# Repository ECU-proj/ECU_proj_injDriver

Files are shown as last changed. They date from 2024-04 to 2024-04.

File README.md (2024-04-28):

# ECU Project

   

The injector driver is an integral part of a broader project aimed at creating a fully customizable Engine Control Unit (ECU). The project’s objective is to provide a versatile tool capable of handling everything from straightforward retrofits to professional scenarios where writing custom software tailored to specific applications is essential. Both the hardware and software components are entirely open source and compatible with professional interfaces, representing the cutting edge in the field of engine and vehicle control

## Dual Injector Driver - Alpha Hardware put in production

The injection stage is a fundamental and delicate component of engine control systems. There are two types of injectors:

High Impedance: Usually, Port Fuel Injection (PFI) injectors have a high-impedance solenoid, which automatically limits the current, albeit at the expense of opening speed and precision.
Low Impedance: Typically, newer Gasoline Direct Injection (GDI) injectors require current control and are more sophisticated. A low impedance driver can drive an high impedance injector with simpler software



The driver mainly focus on injectors, while it will used in other applications also, such as GDI pumps actuations, trasmission solenoids, ....

### Injector Driver Hardware

The injector driver hardware is based on the new TI H-Bridge IC DRV8262 controlled by an Attiny 1624
The driver is capable of 70V and 8A peak in dual configuration (two injectors per driver), which is more than enough for the injectors I had experience on.
The board features a high/low voltage switch for correctly implementing the V boost logic. As the supply switch is in common, controlling the voltage on both the injectors in the same time is not possible. Injection number must be carefully assigned in order to avoid control overlap




### Injector Driver Software

Input: logic pulse corresponding to Injection time from ecu
Output: PID control of the current through the injectors

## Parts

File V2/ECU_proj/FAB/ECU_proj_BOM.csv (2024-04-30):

Id | Riferimento | Impronta | Quantità | Valore | Produttore
1 | J1 | MountingHole_3.2mm_M3_ISO7380_Pad_TopBottom | 1 | OUT1
2 | C12,C14 | C_0402_1005Metric | 2 | 4.7uF
3 | Q1,Q2 | IRF9530NSTRLPBF | 2 | IRF9530NSTRLPBF
4 | C13,C10 | C_0402_1005Metric | 2 | 0.1uF
5 | J9 | MountingHole_3.2mm_M3_ISO7380_Pad_TopBottom | 1 | 48V
6 | U1 | SOIC-14_3.9x8.7mm_P1.27mm | 1 | ATtiny1624-SS
7 | C23 | C_0402_1005Metric | 1 | 1uF
8 | C17,C11,C20,C15,C16,C19,C18,C21 | C_0402_1005Metric | 8 | 10uF
9 | R6,R5 | C_0402_1005Metric | 2 | 1.6k
10 | J10 | PinHeader_2x03_P1.27mm_Vertical | 1 | Conn_02x03_Odd_Even
11 | D2 | LED_0402_1005Metric | 1 | LED
12 | C5,C8,C3,C7,C4,C2 | C_0402_1005Metric | 6 | 1nF 100V
13 | J2 | MountingHole_3.2mm_M3_ISO7380_Pad_TopBottom | 1 | OUT2
14 | J5 | MountingHole_3.2mm_M3_ISO7380_Pad_TopBottom | 1 | GND
15 | J7 | MountingHole_3.2mm_M3_ISO7380_Pad_TopBottom | 1 | 3.3V
16 | C1,C6 | C_0402_1005Metric | 2 | 10nF 100V
17 | IC2 | TC4422SOIC127P600X175-8N | 1 | TC4421AVOA
18 | C22 | CP_Elec_8x11.9 | 1 | C_Polarized
19 | J3 | MountingHole_3.2mm_M3_ISO7380_Pad_TopBottom | 1 | OUT4
20 | C9,C25 | C_0402_1005Metric | 2 | 100nF 100V
21 | C24 | C_0402_1005Metric | 1 | 1uF 100V
22 | J4 | MountingHole_3.2mm_M3_ISO7380_Pad_TopBottom | 1 | OUT3
23 | D1 | V20DM100C | 1 | V20DM100C-M3_I
24 | J8 | MountingHole_3.2mm_M3_ISO7380_Pad_TopBottom | 1 | 12V
25 | R3,R1 | C_0402_1005Metric | 2 | 0.75
26 | IC1 | DRV8262 | 1 | DRV8262DDWR
27 | IC3 | TC4422SOIC127P600X175-8N | 1 | TC4422AVOA
28 | J11 | PinHeader_1x01_P1.00mm_Vertical | 1 | Conn_01x01
29 | J6 | MountingHole_3.2mm_M3_ISO7380_Pad_TopBottom | 1 | PGND
30 | R2,R4 | C_0402_1005Metric | 2 | 100k
31 | R7 | C_0402_1005Metric | 1 | 10k

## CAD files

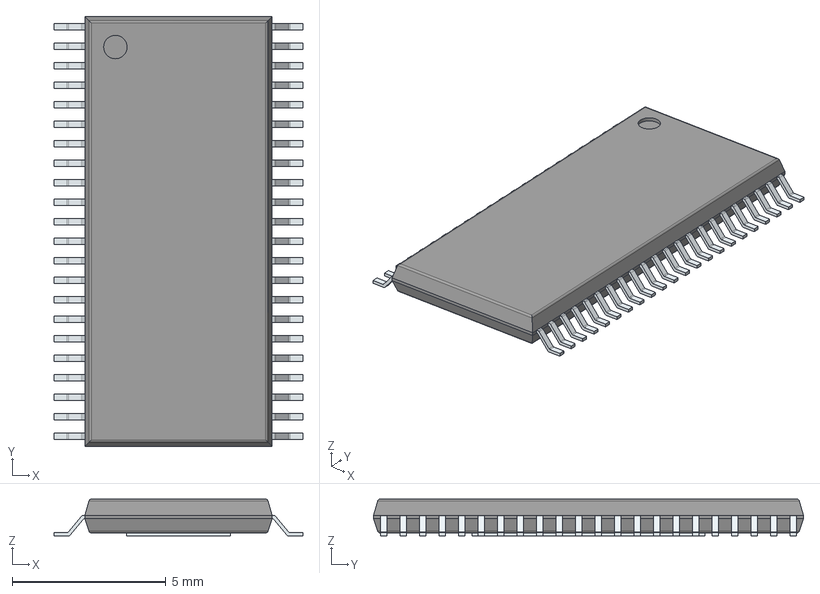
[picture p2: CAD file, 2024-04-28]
V2/LIB_DRV8262DDWR/DRV8262DDWR/3D/DRV8262DDWR.stp
8.10 x 14.0 x 1.20 mm
PinsArrayLR
ThermalPad

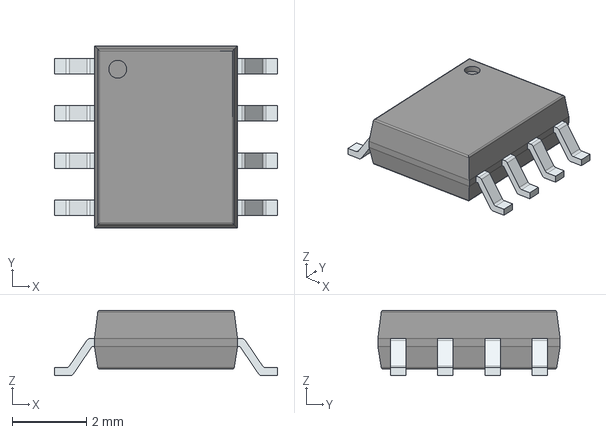
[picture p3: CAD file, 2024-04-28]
V2/LIB_TC4422AVOA/TC4422AVOA/3D/TC4422AVOA.stp
6.00 x 4.90 x 1.75 mm
PinsArrayLR

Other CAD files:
V2/LIB_DRV8262DDWR/DRV8262DDWR/Allegro/sop64p810x120-45n.psm
V2/LIB_DRV8262DDWR/DRV8262DDWR/DEHDL/drv8262ddwr/chips/chips.prt
V2/LIB_IRF9530NSTRLPBF/IRF9530NSTRLPBF/Allegro/irf9530nstrlpbf.psm
V2/LIB_IRF9530NSTRLPBF/IRF9530NSTRLPBF/DEHDL/irf9530nstrlpbf/chips/chips.prt
V2/LIB_TC4422AVOA/TC4422AVOA/Allegro/soic127p600x175-8n.psm
V2/LIB_TC4422AVOA/TC4422AVOA/DEHDL/tc4422avoa/chips/chips.prt
V2/LIB_V20DM100C-M3_I/V20DM100C-M3_I/Allegro/v40dl45bpm3i.psm
V2/LIB_V20DM100C-M3_I/V20DM100C-M3_I/DEHDL/v20dm100c_m3_i/chips/chips.prt

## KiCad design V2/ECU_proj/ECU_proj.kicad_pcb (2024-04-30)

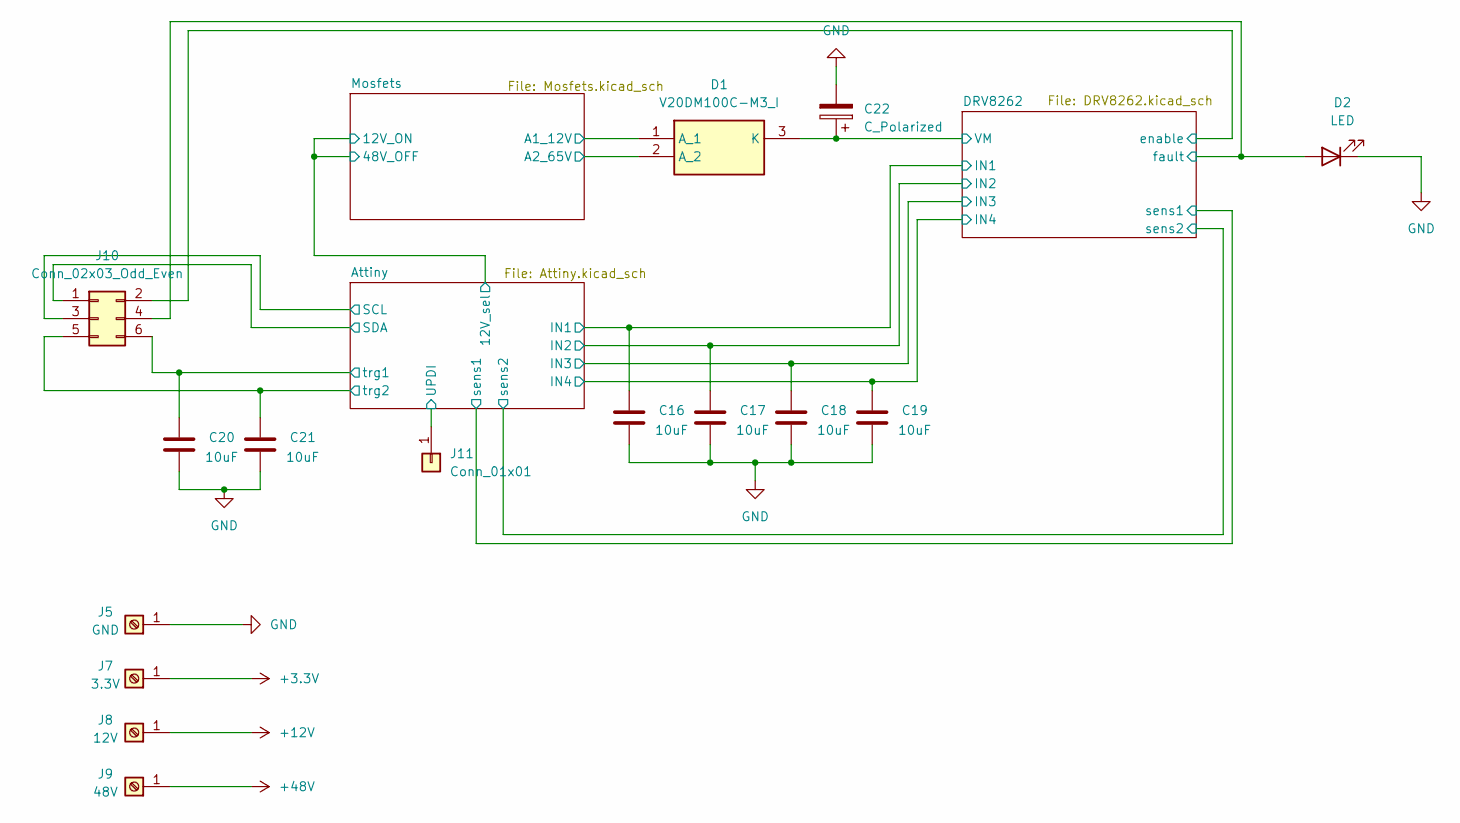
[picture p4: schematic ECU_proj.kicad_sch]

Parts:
C16, C17, C18, C19, C20, C21: 10uF; C_0402_1005Metric
C22: C_Polarized; CP_Elec_8x11.9
D1: V20DM100C-M3_I; V20DM100C; Mouser Part Number 78-V20DM100C-M3/I
D2: LED; LED_0402_1005Metric
J5: GND; MountingHole_3.2mm_M3_ISO7380_Pad_TopBottom
J7: 3.3V; MountingHole_3.2mm_M3_ISO7380_Pad_TopBottom
J8: 12V; MountingHole_3.2mm_M3_ISO7380_Pad_TopBottom
J9: 48V; MountingHole_3.2mm_M3_ISO7380_Pad_TopBottom
J10: Conn_02x03_Odd_Even; PinHeader_2x03_P1.27mm_Vertical
J11: Conn_01x01; PinHeader_1x01_P1.00mm_Vertical

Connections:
+3.3V: J7.1; also elsewhere on the board
+12V: J8.1; also elsewhere on the board
+48V: J9.1; also elsewhere on the board
/Attiny/IN1: C16.1; also elsewhere on the board
/Attiny/IN2: C17.1; also elsewhere on the board
/Attiny/IN3: C18.1; also elsewhere on the board
/Attiny/IN4: C19.1; also elsewhere on the board
/Attiny/SCL: J10.3; also elsewhere on the board
/Attiny/SDA: J10.1; also elsewhere on the board
/Attiny/UPDI: J11.1; also elsewhere on the board
/Attiny/trg1: C20.1, J10.6; also elsewhere on the board
/Attiny/trg2: C21.1, J10.5; also elsewhere on the board
/DRV8262/VM: C22.1, D1.3 (K); also elsewhere on the board
/DRV8262/enable: J10.2; also elsewhere on the board
/DRV8262/fault: D2.2 (A), J10.4; also elsewhere on the board
/Mosfets/A1_12V: D1.1 (A_1); also elsewhere on the board
/Mosfets/A2_65V: D1.2 (A_2); also elsewhere on the board
GND: C16.2, C17.2, C18.2, C19.2, C20.2, C21.2, C22.2, D2.1 (K), J5.1; also elsewhere on the board

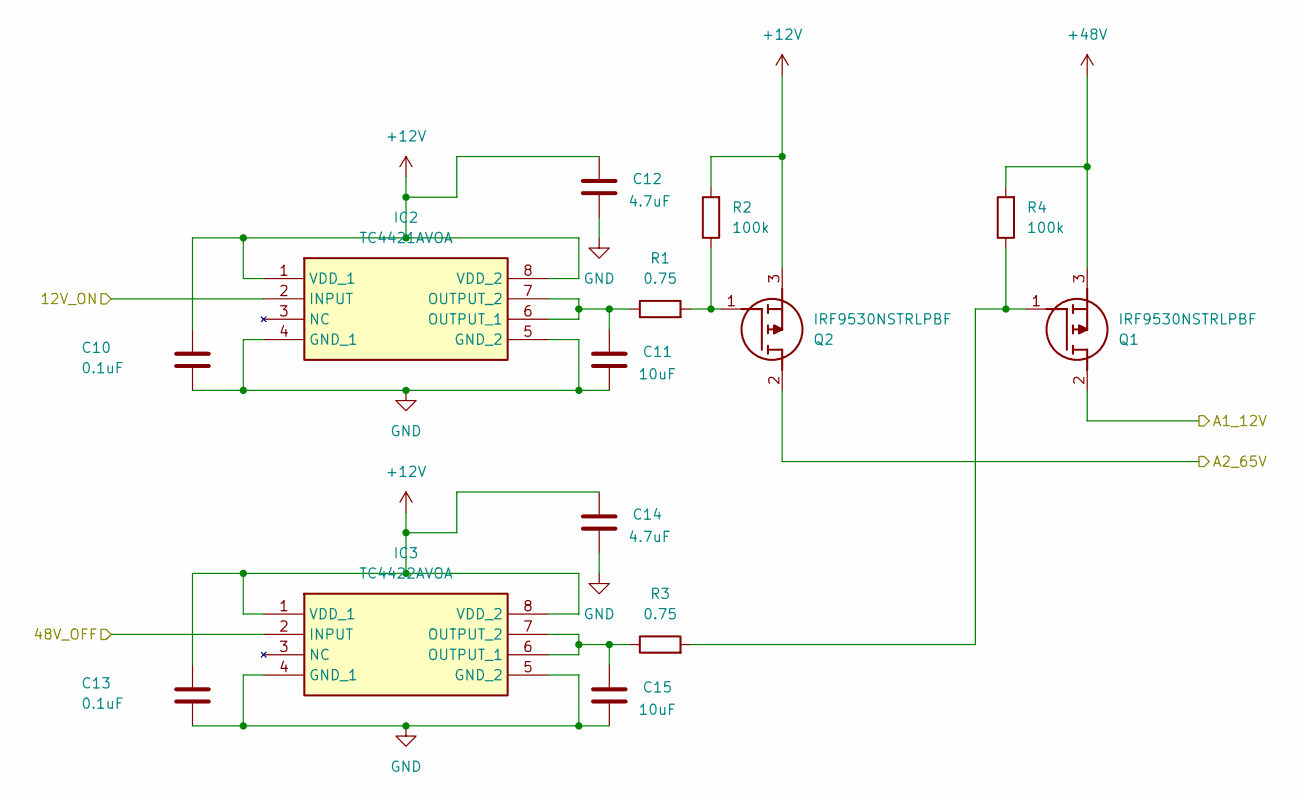
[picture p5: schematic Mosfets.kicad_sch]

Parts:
C10, C13: 0.1uF; C_0402_1005Metric
C11, C15: 10uF; C_0402_1005Metric
C12, C14: 4.7uF; C_0402_1005Metric
IC2: TC4421AVOA; TC4422SOIC127P600X175-8N; Mouser Part Number 579-TC4422AVOA
IC3: TC4422AVOA; TC4422SOIC127P600X175-8N; Mouser Part Number 579-TC4422AVOA
Q1, Q2: IRF9530NSTRLPBF; Mouser Part Number 942-IRF9530NSTRLPBF
R1, R3: 0.75; C_0402_1005Metric
R2, R4: 100k; C_0402_1005Metric

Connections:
+12V: C10.1, C12.1, C13.1, C14.1, IC2.1 (VDD_1), IC2.8 (VDD_2), IC3.1 (VDD_1), IC3.8 (VDD_2), Q2.3 (S), R2.2; also elsewhere on the board
+48V: Q1.3 (S), R4.2; also elsewhere on the board
/Attiny/12V_sel: IC2.2 (INPUT), IC3.2 (INPUT); also elsewhere on the board
/Mosfets/A1_12V: Q1.2 (D); also elsewhere on the board
/Mosfets/A2_65V: Q2.2 (D); also elsewhere on the board
GND: C10.2, C11.2, C12.2, C13.2, C14.2, C15.2, IC2.4 (GND_1), IC2.5 (GND_2), IC3.4 (GND_1), IC3.5 (GND_2); also elsewhere on the board
unnamed: C11.1, IC2.6 (OUTPUT_1), IC2.7 (OUTPUT_2), R1.1
unnamed: C15.1, IC3.6 (OUTPUT_1), IC3.7 (OUTPUT_2), R3.1
unnamed: Q1.1 (G), R3.2, R4.1
unnamed: Q2.1 (G), R1.2, R2.1

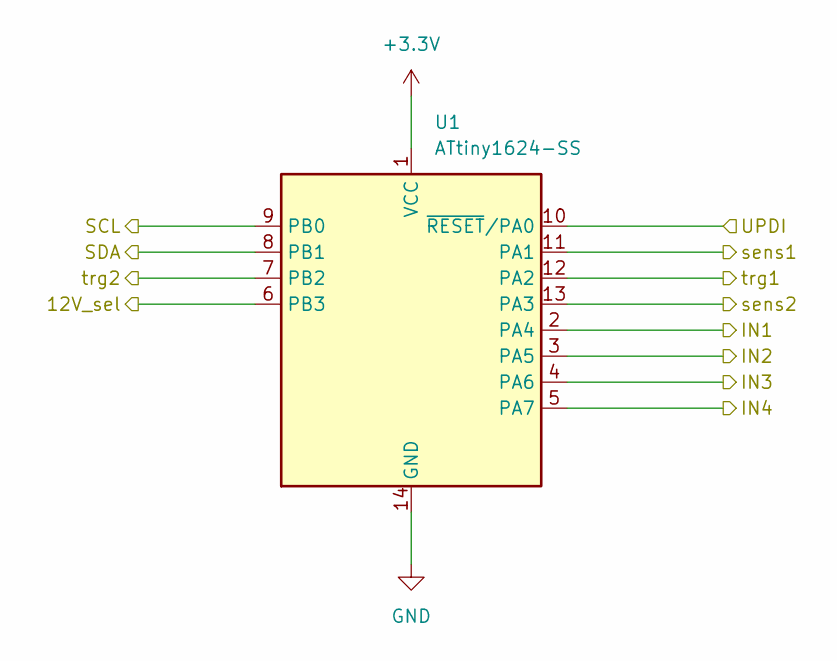
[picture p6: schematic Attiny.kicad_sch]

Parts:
U1: ATtiny1624-SS; SOIC-14_3.9x8.7mm_P1.27mm

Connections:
+3.3V: U1.1 (VCC); also elsewhere on the board
/Attiny/12V_sel: U1.6 (PB3); also elsewhere on the board
/Attiny/IN1: U1.2 (PA4); also elsewhere on the board
/Attiny/IN2: U1.3 (PA5); also elsewhere on the board
/Attiny/IN3: U1.4 (PA6); also elsewhere on the board
/Attiny/IN4: U1.5 (PA7); also elsewhere on the board
/Attiny/SCL: U1.9 (PB0); also elsewhere on the board
/Attiny/SDA: U1.8 (PB1); also elsewhere on the board
/Attiny/UPDI: U1.10 (~RESET/PA0); also elsewhere on the board
/Attiny/sens1: U1.11 (PA1); also elsewhere on the board
/Attiny/sens2: U1.13 (PA3); also elsewhere on the board
/Attiny/trg1: U1.12 (PA2); also elsewhere on the board
/Attiny/trg2: U1.7 (PB2); also elsewhere on the board
GND: U1.14 (GND); also elsewhere on the board

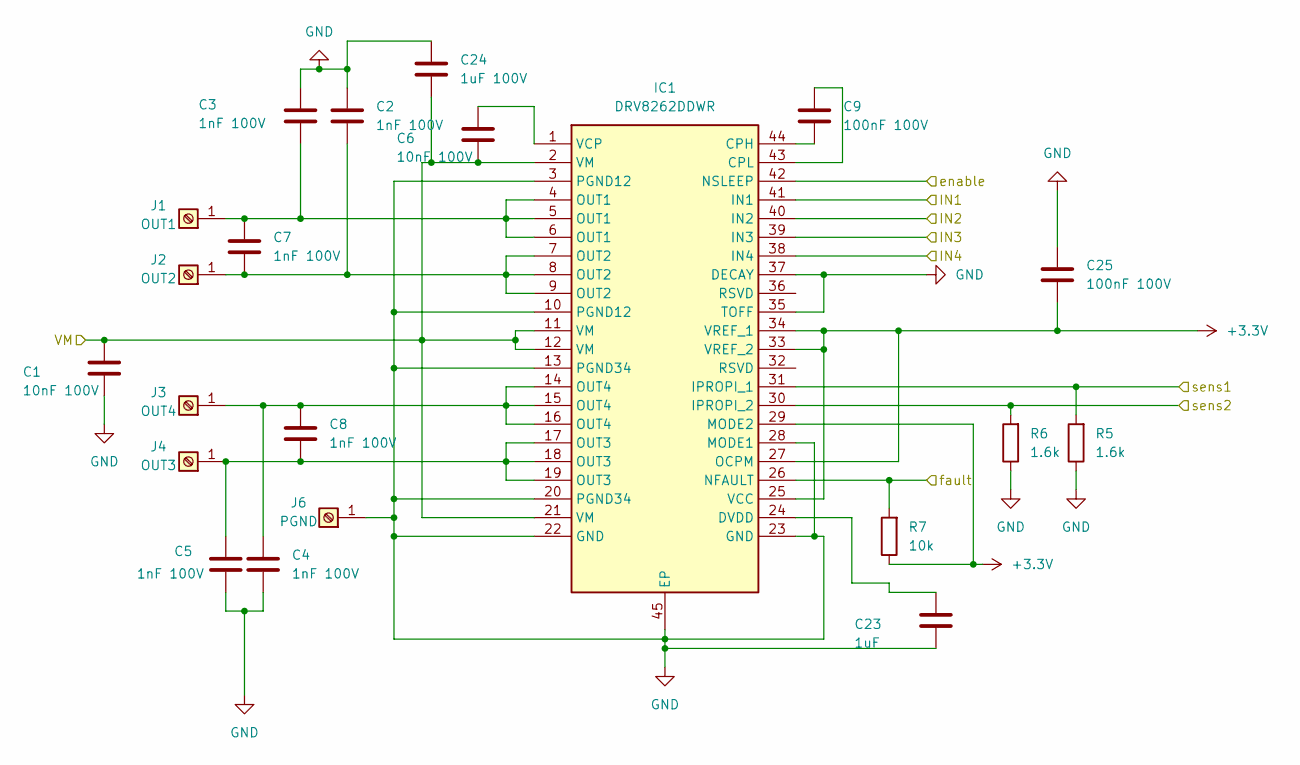
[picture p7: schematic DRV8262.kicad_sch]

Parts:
C1, C6: 10nF 100V; C_0402_1005Metric
C2, C3, C4, C5, C7, C8: 1nF 100V; C_0402_1005Metric
C9, C25: 100nF 100V; C_0402_1005Metric
C23: 1uF; C_0402_1005Metric
C24: 1uF 100V; C_0402_1005Metric
IC1: DRV8262DDWR; DRV8262; Mouser Part Number 595-DRV8262DDWR
J1: OUT1; MountingHole_3.2mm_M3_ISO7380_Pad_TopBottom
J2: OUT2; MountingHole_3.2mm_M3_ISO7380_Pad_TopBottom
J3: OUT4; MountingHole_3.2mm_M3_ISO7380_Pad_TopBottom
J4: OUT3; MountingHole_3.2mm_M3_ISO7380_Pad_TopBottom
J6: PGND; MountingHole_3.2mm_M3_ISO7380_Pad_TopBottom
R5, R6: 1.6k; C_0402_1005Metric
R7: 10k; C_0402_1005Metric

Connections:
+3.3V: C25.2, IC1.25 (VCC), IC1.27 (OCPM), IC1.29 (MODE2), IC1.33 (VREF_2), IC1.34 (VREF_1), R7.1; also elsewhere on the board
/Attiny/IN1: IC1.41 (IN1); also elsewhere on the board
/Attiny/IN2: IC1.40 (IN2); also elsewhere on the board
/Attiny/IN3: IC1.39 (IN3); also elsewhere on the board
/Attiny/IN4: IC1.38 (IN4); also elsewhere on the board
/Attiny/sens1: IC1.31 (IPROPI_1), R5.2; also elsewhere on the board
/Attiny/sens2: IC1.30 (IPROPI_2), R6.2; also elsewhere on the board
/DRV8262/VM: C1.1, C6.2, C24.2, IC1.2 (VM), IC1.11 (VM), IC1.12 (VM), IC1.21 (VM); also elsewhere on the board
/DRV8262/enable: IC1.42 (NSLEEP); also elsewhere on the board
/DRV8262/fault: IC1.26 (NFAULT), R7.2; also elsewhere on the board
GND: C1.2, C2.1, C3.1, C4.2, C5.2, C23.2, C24.1, C25.1, IC1.3 (PGND12), IC1.10 (PGND12), IC1.13 (PGND34), IC1.20 (PGND34), IC1.22 (GND), IC1.23 (GND), IC1.28 (MODE1), IC1.35 (TOFF), IC1.37 (DECAY), IC1.45 (EP), J6.1, R5.1, R6.1; also elsewhere on the board
unnamed: C9.2, IC1.44 (CPH)
unnamed: C9.1, IC1.43 (CPL)
unnamed: C23.1, IC1.24 (DVDD)
unnamed: C6.1, IC1.1 (VCP)
unnamed: C3.2, C7.1, IC1.4 (OUT1), IC1.5 (OUT1), IC1.6 (OUT1), J1.1
unnamed: C2.2, C7.2, IC1.7 (OUT2), IC1.8 (OUT2), IC1.9 (OUT2), J2.1
unnamed: C4.1, C8.1, IC1.14 (OUT4), IC1.15 (OUT4), IC1.16 (OUT4), J3.1
unnamed: C5.1, C8.2, IC1.17 (OUT3), IC1.18 (OUT3), IC1.19 (OUT3), J4.1

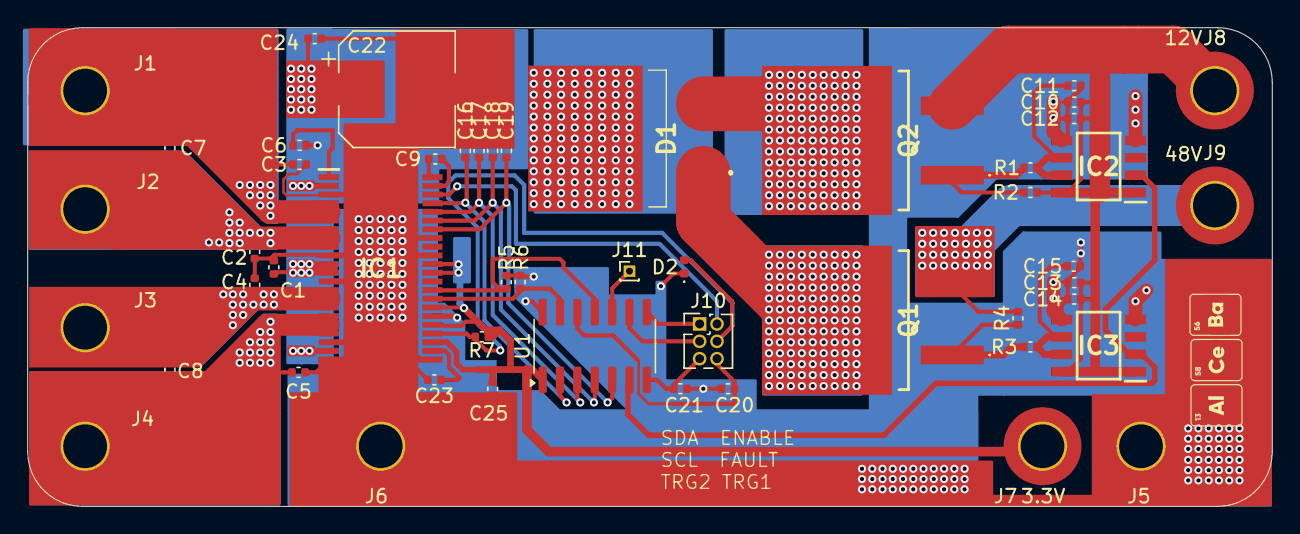
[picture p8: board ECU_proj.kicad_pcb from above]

Board: 2 copper layers, 91.0 x 35.0 mm, 51 parts (0 on the bottom side), 33 nets.

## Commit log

2024-04-28 First Release
    [Attiny.kicad_sch, DRV8262.kicad_sch, DRV8262DDWR.stp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]
2024-04-29 Review before PCB production
    [ECU_proj-B_Cu.gbr, ECU_proj-B_Mask.gbr, ECU_proj-B_Paste.gbr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]
2024-04-30 Alpha Release
    [DRV8262.kicad_sch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]
